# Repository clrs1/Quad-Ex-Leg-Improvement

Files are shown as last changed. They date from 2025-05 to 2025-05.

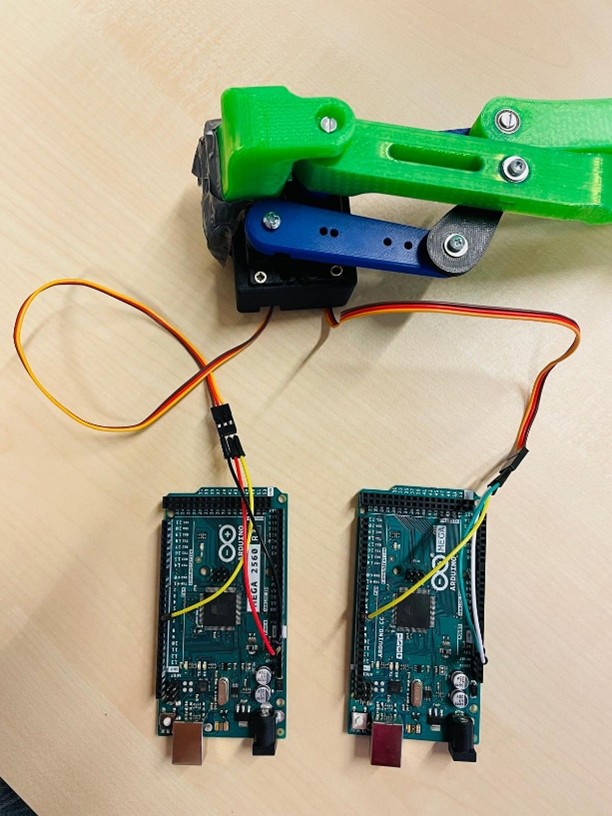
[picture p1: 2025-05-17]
Test set up.jpg

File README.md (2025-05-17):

# Quad-Ex-Leg-Improvement
This repository contains the Fusion 360 design, sliced print files, and test setup for the Quad-Ex leg improvements (Prototyping May 2025). The improvements focus on reducing play by adding side pockets and extra bearings to the original design. Below is a description of how to assemble the Quad-Ex leg.

Design folder:
- Fusion 360 design, sliced print files, and 3D-printing settings.
- Note that the hole for the servo arm horns must be created before printing the servo arm, as it is not yet included in the sliced print file.

Test set up: 
- The test for a single leg was done with two servomotors using two separate Arduino MEGA 2560 (image and code provided).
- If a 6x AA battery holder is available, the test set up with the Arduino UNO R3 with KS0470 Keyestudio servo shield for two servomotors is recommended.
    - KS0470 Keyestudio servo shield: https://wiki.keyestudio.com/KS0470_Keyestudio_4WD_BT_Robot_Car_V2.0_Kit_for_Arduino
    - Tutorial test set up:  https://www.youtube.com/watch?v=TkA2LJctU1c

Assembly leg:

To assemble the remaining 3 legs with the improved design, the parts must
 be printed and supports removed. This is most easily done with a box cutter.
 For the 2 legs on the opposite side of the Quad-Ex, the designs must be flipped
 before printing to ensure they are properly mirrored.
 
 Bearings with an inner diameter of 3 mm, an outer diameter of 10 mm, and
 a length of 4 mm must be fitted in each of the 9 side pockets. The screws
 and bolts are each 3 mm in diameter. Side pockets of 6.3 x 2.4 mm were added to the design, where a nut of
 2-mm in length must be inserted into the hole before a bolt can be added. It is
 important to add small metal disks between every point where there would be
 plastic on plastic contact as this reduces deformation and mechanical play.

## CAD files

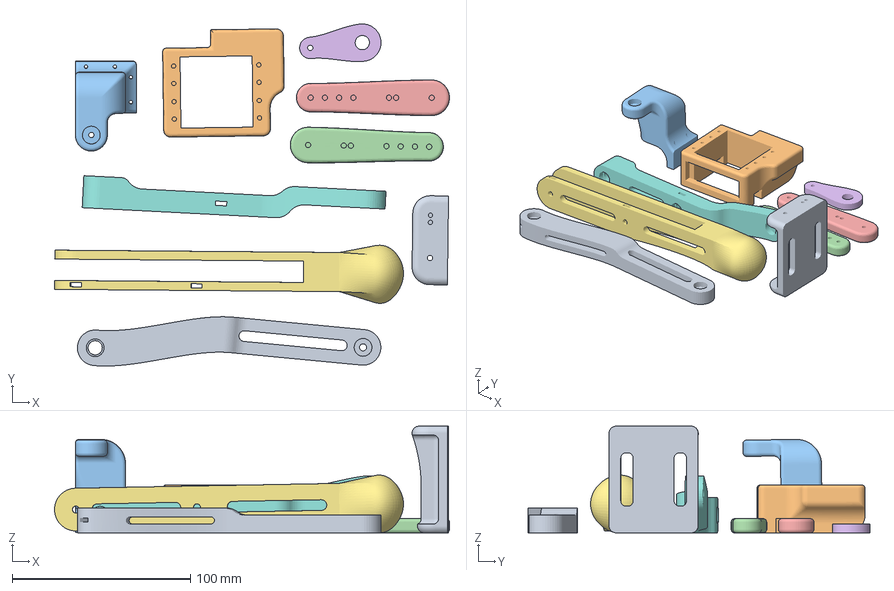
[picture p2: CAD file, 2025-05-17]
Quad-Ex improved single leg.3mf
221.9 x 192.2 x 60.0 mm
Leg 1 - 15 extension servo housing v2.stl
Leg 1 - 15 servo housing v2.stl
Leg 1 - 40 hip joint v2.stl
Leg 1 - 40 servo extension 2 v2.stl
Leg 1 - 40 servo extension v2.stl
Leg 1 - 40 small thing v2.stl
Leg 1 - 15 tibia v2.stl
Leg 1 - 15 large linkage v2.stl
Leg 1 - 15 fibula v2.stl

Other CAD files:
Fusion 360 Quad-Ex improved single leg design.f3d

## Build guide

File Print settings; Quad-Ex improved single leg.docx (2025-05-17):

# Print settings: Quad-Ex improved single leg

Support
Supports | For support enforcers only
Generate support material | Ticked off
Interface pattern | Rectilinear
Pattern spacing | 4 mm
Overhang threshold | 45 degrees

Print settings
Infill – servo horn extensions, link, hip holder | 40 %
Infill rest leg components | 15-20%
Infill pattern | Gyroid
Outer wall | Thicker – refer to original Quad-Ex documentation

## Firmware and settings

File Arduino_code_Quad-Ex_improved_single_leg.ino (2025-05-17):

#include <Servo.h>

Servo myServo;  // Maak een servo-object aan

void setup() {
  myServo.attach(6);  // Sluit de servo aan op pin 6 
  myServo.write(0);
}

void loop() {
  // Beweeg van 0 naar 180 graden
  for (int pos = 100; pos <= 160; pos++) {
    myServo.write(pos);   // Zet de hoek
    delay(10);            // Kleine pauze voor vloeiende beweging
  }
  
  // Beweeg van 180 terug naar 0 graden
  for (int pos = 160; pos >= 100; pos--) {
    myServo.write(pos);   // Zet de hoek
    delay(10);            // Kleine pauze voor vloeiende beweging
  }
}

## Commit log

2025-05-17 Create Fusion 360 Quad-Ex improved single leg design
2025-05-17 Create Arduino_code_Quad-Ex_improved_single_leg
